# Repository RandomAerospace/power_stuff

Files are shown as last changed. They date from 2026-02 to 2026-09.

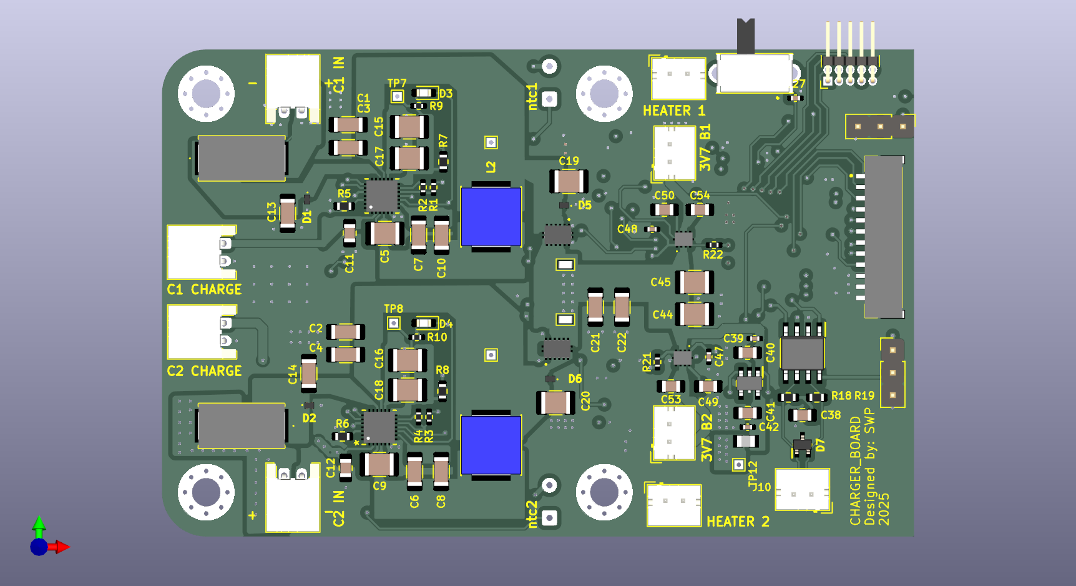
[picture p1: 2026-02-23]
POWER_DISTRIBUTION/SOLAR CHARGER/IMAGES AND RENDERS/SOLAR CHARGER-Top.png

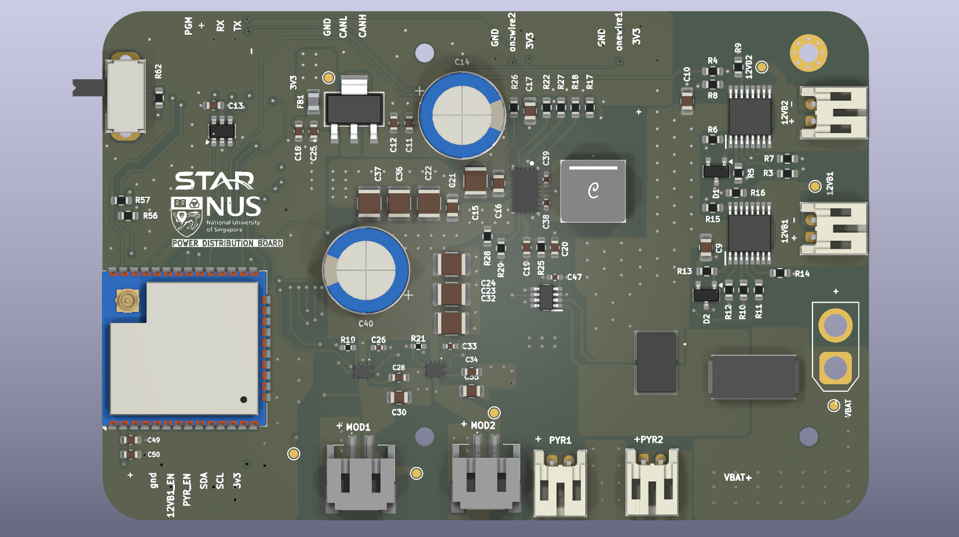
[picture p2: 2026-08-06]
POWER_DISTRIBUTION/UREX_PDB/UREX_PDB/FRONT_PDBr1.png

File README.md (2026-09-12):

if you want to add more stuff, use library loader and set path of downloaded footprints to SAMACSYS_LIB_PDB on my repo!
additionally, please set path preferences based on relative path of the folder that you have pulled the github repo into.
Go to UREX PDB  folder under POWER DISTRIBUTION for the pimped up weather balloon PDB

Power board presentation:https://drive.google.com/file/d/1bSlgJGe3XdCi3mun8Qso9A9fgnM_BNgd/view?usp=sharing

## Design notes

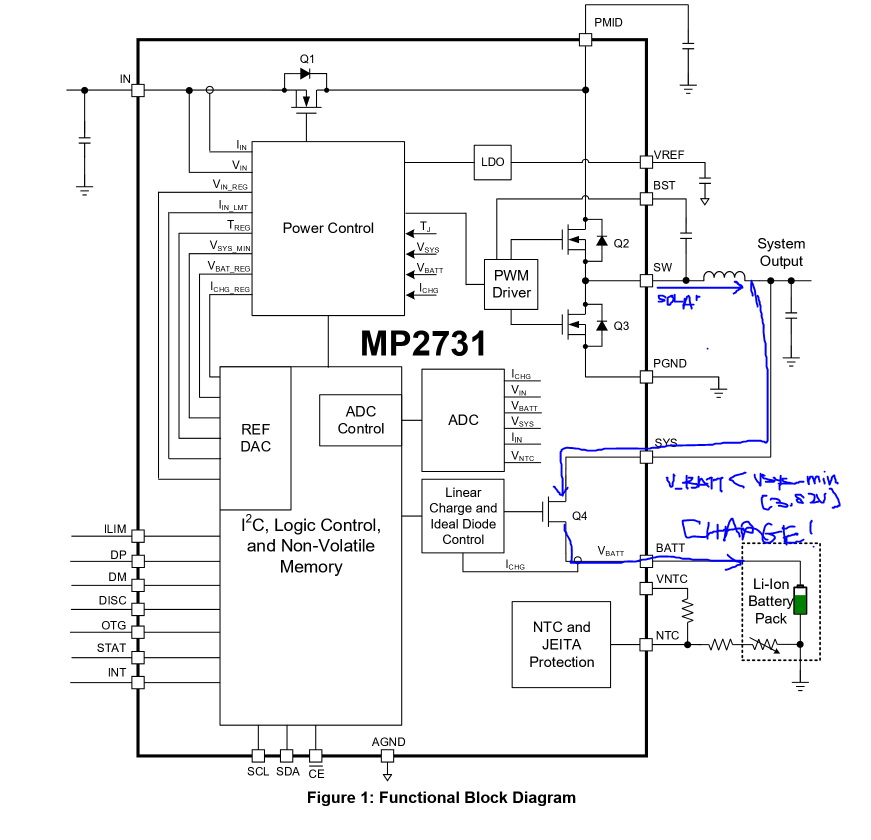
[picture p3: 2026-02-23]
DATASHEETS/CHARGE!.PNG

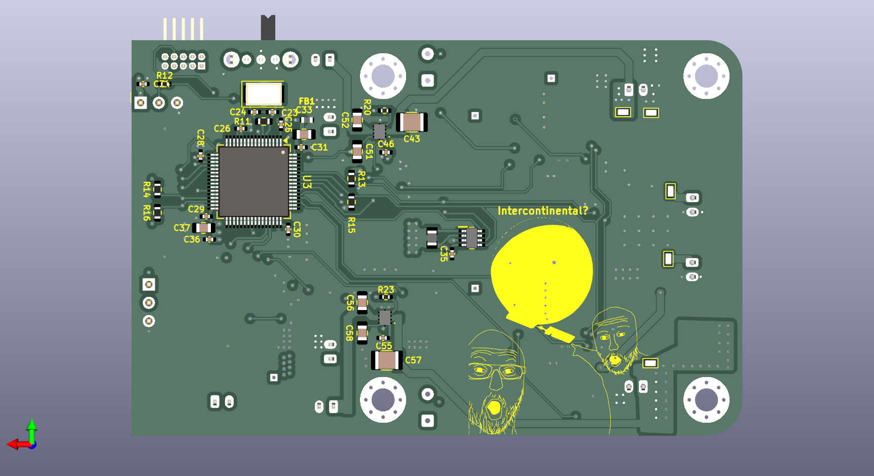
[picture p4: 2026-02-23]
POWER_DISTRIBUTION/SOLAR CHARGER/IMAGES AND RENDERS/SOLAR CHARGER-bottom.png

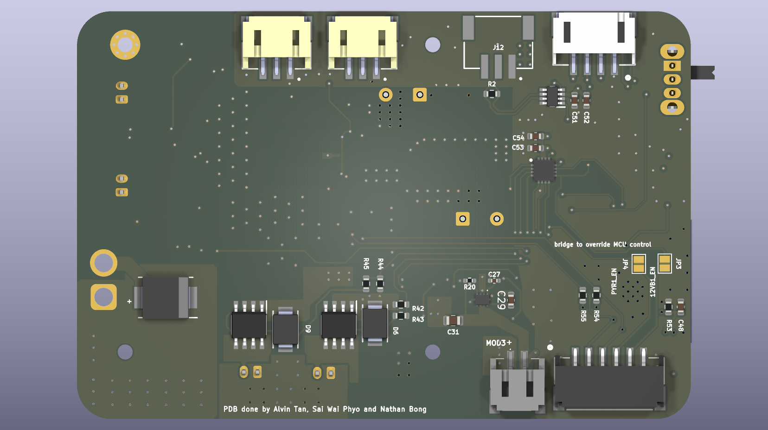
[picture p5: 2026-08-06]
POWER_DISTRIBUTION/UREX_PDB/UREX_PDB/BACK_PDBr1.png

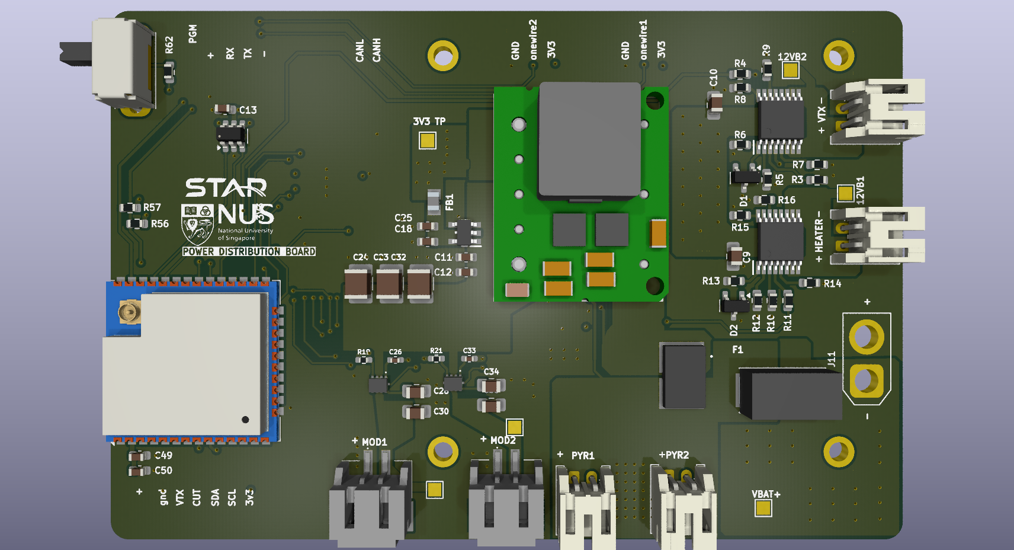
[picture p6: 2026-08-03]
POWER_DISTRIBUTION/UREX_PDB/UREX_PDB/BACK__PDB.png

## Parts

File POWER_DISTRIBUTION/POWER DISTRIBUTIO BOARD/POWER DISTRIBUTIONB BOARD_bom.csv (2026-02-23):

Id | Designator | Footprint | Quantity | Designation | Supplier and ref
1 | TP4,TP5,TP3,TP6,TP8,TP24,TP7 | S175146R | 7 | S1751-46R
2 | F2,F1,F3 | 0154001.DRT | 3 | 0154010.DR
3 | C31,C34,C33,C32 | C_Radial_D6.3mm_H5.0mm_P2.50mm | 4 | 47u
4 | J25,J26,J28,J27 | XT90PWF | 4 | XT90PW-F
5 | J7,J4,J1 | AMASS_XT60-F_1x02_P7.20mm_Vertical | 3 | Conn_01x02_Socket
6 | PS3,PS4 | RPMA5080OF | 2 | RPMA5.0-8.0_OF
7 | U3,U2 | 17861650002 | 2 | 178.6165.0002
8 | R52 | R_0805_2012Metric_Pad1.20x1.40mm_HandSolder | 1 | 8k66
9 | R51 | R_0805_2012Metric_Pad1.20x1.40mm_HandSolder | 1 | 1k82

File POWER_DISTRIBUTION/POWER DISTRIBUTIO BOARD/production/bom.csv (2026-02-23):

Designator | Footprint | Quantity | Value | LCSC Part #
C31, C32, C33, C34 | C_Radial_D6.3mm_H5.0mm_P2.50mm | 4 | 47u
F1, F2, F3 | 0154001.DRT | 3 | 0154010.DR
J1, J4, J7 | AMASS_XT60-F_1x02_P7.20mm_Vertical | 3 | Conn_01x02_Socket
J25, J26, J27, J28 | XT90PWF | 4 | XT90PW-F
PS3, PS4 | RPMA5080OF | 2 | RPMA5.0-8.0_OF
R51 | 0805 | 1 | 1k82
R52 | 0805 | 1 | 8k66
TP24, TP3, TP4, TP5, TP6, TP7, TP8 | S175146R | 7 | S1751-46R
U2, U3 | 17861650002 | 2 | 178.6165.0002

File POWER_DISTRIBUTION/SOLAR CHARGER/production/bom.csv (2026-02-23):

Designator | Footprint | Quantity | Value | LCSC Part #
C1, C10, C13, C14, C2, C21, C22, C3, C4, C6, C7, C8 | 1206 | 12 | 47uF @16VDC
C11, C12, C33, C37, C38, C40, C41, C49, C50, C51, C52, C53, C54, C56, C58 | 0805 | 15 | 1uF @50V
C15, C16, C17, C18, C19, C20, C43, C44, C45, C5, C57, C9 | 1210 | 12 | 10uF @50V
C23, C24 | 0402 | 2 | 20p
C25, C26, C27, C28, C29, C30, C31, C34, C35, C36, C39, C42, C46, C47, C48, C55 | 0402 | 16 | 100nF @50V
D1, D2, D5, D6 | PESD5V0S1BL315 | 4 | PTVS3V3D1BALYL
D3, D4 | 0603 | 2 | LED
D7 | SOT65P210X110-3N | 1 | PESD2CANFD24V-UX
F1, F2 | 0154005DR | 2 | 0154005.DR
FB1 | BLM18SP221SN1B | 1 | BLM18AG601SN1D
FB2 | BEADC2012X105N | 1 | BLM21PG221SN1D
IC1, IC2 | LTC4451AVTRMPBF | 2 | LTC4451AV#TRMPBF
IC3 | SOT65P280X110-8N | 1 | INA232AIDDFR
IC4 | SOIC127P600X175-8N | 1 | SN65HVD233QDRQ1
IC5, IC6, IC7, IC8 | TPS22997RYZR | 4 | TPS22997RYZR
J1 | PinHeader_1x03_P2.54mm_Vertical | 1 | Conn_01x03_Socket
J10, J12, J13, J14, J15 | JST_PH_B2B-PH-K_1x02_P2.00mm_Vertical | 5 | Conn_01x02
J11 | PinHeader_1x03_P2.54mm_Vertical | 1 | Conn_01x03
J18 | BM12BGHSTBTLFSN | 1 | BM12B-GHS-TBT_LF__SN_
J2 | PinHeader_2x05_P1.27mm_Horizontal | 1 | Conn_ARM_JTAG_SWD_10
J3, J5, J6, J7 | JST_PH_S2B-PH-K_1x02_P2.00mm_Horizontal | 4 | Conn_01x02
J8, J9 | SolderWire-0.127sqmm_1x02_P3.7mm_D0.48mm_OD1mm | 2 | Conn_01x02
L1, L2 | INDPM6868X420N | 2 | SRR6838A-1R0Y
PS1 | SOT95P280X145-5N | 1 | TLV75733PDBVR
R1, R10, R12, R2, R20, R21, R22, R23, R3, R4, R9 | 0402 | 11 | 10k
R11 | 0603 | 1 | 1M
R13, R14, R15, R16 | 0603 | 4 | 2.4k
R17 | RESC2013X58N | 1 | WSLP08059L000FEA18
R18, R19 | 0603 | 2 | 60
R5, R6 | 0603 | 2 | 20K
R7, R8 | 0603 | 2 | 100K
S1 | OS102011MA1QN1 | 1 | OS102011MA1QN1
TP1, TP12, TP2, TP7, TP8 | TestPoint_THTPad_1.0x1.0mm_Drill0.5mm | 5 | TestPoint_Alt
TP10, TP11, TP14, TP15, TP16, TP17, TP9 | S276146R | 7 | S2761-46R
U1, U2 | QFN-26_MP2731 | 2 | MP2731GQC-0000-P
U3 | LQFP-64_10x10mm_P0.5mm | 1 | STM32F103RGTx
Y1 | Crystal_SMD_5032-2Pin_5.0x3.2mm | 1 | Crystal

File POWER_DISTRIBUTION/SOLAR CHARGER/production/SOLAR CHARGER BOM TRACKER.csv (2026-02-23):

 | Mouser No | Mfr. No | Manufacturer | Customer No | Description | RoHS | Lifecycle | Order Qty. | Price (SGD) | Ext.: (SGD)
1 | 81-GRM1555C1H200GA1D | GRM1555C1H200GA01D | Murata |  | Multilayer Ceramic Capacitors MLCC - SMD/SMT 20 pF 50 VDC 2% 0402 C0G (NP0) | RoHS Compliant |  | 100 | $0.051 | $5.10
2 | 81-GRM155R61H104KE9J | GRM155R61H104KE19J | Murata |  | Multilayer Ceramic Capacitors MLCC - SMD/SMT 0.1 uF 50 VDC 10% 0402 X5R | RoHS Compliant |  | 500 | $0.025 | $12.50
3 | 81-GRT21BR71H105KE1K | GRT21BR71H105KE01K | Murata |  | Multilayer Ceramic Capacitors MLCC - SMD/SMT 1 uF 50 VDC 10% 0805 X7R AEC-Q200 |  |  | 100 | $0.097 | $9.70
4 | 71-WSLP08059L000FEA1 | WSLP08059L000FEA18 | Vishay |  | Current Sense Resistors - SMD 1watt 0.009ohm 1% | RoHS Compliant |  | 10 | $1.43 | $14.30
5 | 652-SRR6838A-1R0Y | SRR6838A-1R0Y | Bourns |  | Power Inductors - SMD Ind,6.8x6.8x3.8mm,1uH+/-30%,4.5A, | RoHS Compliant | New Product | 10 | $1.60 | $16.00
6 | 595-INA232AIDDFR | INA232AIDDFR | Texas Instruments |  | Current & Power Monitors & Regulators 48-V 16-bit high-pr ecision I C output d | RoHS Compliant |  | 10 | $1.85 | $18.50
7 | 595-TPS22997RYZR | TPS22997RYZR | Texas Instruments |  | Power Switch ICs - Power Distribution 5.5-V 10-A 4-mohm on -resistance load swi | RoHS Compliant |  | 5 | $1.04 | $5.20

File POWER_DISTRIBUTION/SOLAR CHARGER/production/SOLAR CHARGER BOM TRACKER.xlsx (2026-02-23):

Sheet: SOLAR CHARGER_BOM
Reference | Value | Footprint | Datasheet | Qty | DNP | Exclude from BOM | Exclude from Board
R7,R8 | CRCW0603100KFKEA | Resistor_SMD:R_0603_1608Metric | 100K | 2
R1,R2,R3,R4,R9,R10,R12,R20,R21,R22,R23 | CRCW040210K0FKED | Resistor_SMD:R_0402_1005Metric_Pad0.72x0.64mm_HandSolder | 10k | 11
C23,C24 | GRM1555C1H200GA01D | Capacitor_SMD:C_0402_1005Metric_Pad0.74x0.62mm_HandSolder | 20p | 2
C25,C26,C27,C28,C29,C30,C31,C34,C35,C36,C39,C42,C46,C47,C48,C55 | GRM155R61H104KE19J | Capacitor_SMD:C_0402_1005Metric_Pad0.74x0.62mm_HandSolder | 100nF @50V | 16
C1,C2,C3,C4,C6,C7,C8,C10,C13,C14,C21,C22 | GRM31CR61C476ME44L | Capacitor_SMD:C_1206_3216Metric_Pad1.33x1.80mm_HandSolder | 47uF @16VDC | 12
C5,C9,C15,C16,C17,C18,C19,C20,C43,C44,C45,C57 | GRM32EC72A106KE05L | Capacitor_SMD:C_1210_3225Metric_Pad1.33x2.70mm_HandSolder | 10uF @50V | 12
C11,C12,C33,C37,C38,C40,C41,C49,C50,C51,C52,C53,C54,C56,C58 | GRT21BR71H105KE01K | Capacitor_SMD:C_0805_2012Metric_Pad1.18x1.45mm_HandSolder | 1uF @50V | 15
J2 | Conn_ARM_JTAG_SWD_10 | Connector_PinHeader_1.27mm:PinHeader_2x05_P1.27mm_Horizontal | http://infocenter.arm.com/help/topic/com.arm.doc.ddi0314h/DDI0314H_coresight_components_trm.pdf | 1
J18 | BM12B-GHS-TBT_LF__SN_ | samac_sys:BM12BGHSTBTLFSN | http://www.jst-mfg.com/product/pdf/eng/eGH.pdf | 1
FB1 | BLM18AG601SN1D | samac_sys:BLM18SP221SN1B | http://www.murata.com/~/media/webrenewal/support/library/catalog/products/emc/emifil/c31e.ashx?la=en-gb | 1
IC4 | SN65HVD233QDRQ1 | samac_sys:SOIC127P600X175-8N | http://www.ti.com/lit/gpn/sn65hvd233-q1 | 1
PS1 | TLV75733PDBVR | samac_sys:SOT95P280X145-5N | http://www.ti.com/lit/gpn/tlv757p | 1
D7 | PESD2CANFD24V-UX | samac_sys:SOT65P210X110-3N | https://assets.nexperia.com/documents/data-sheet/PESD2CANFD24V-U.pdf | 1
D1,D2,D5,D6 | PTVS3V3D1BALYL | samac_sys:PESD5V0S1BL315 | https://assets.nexperia.com/documents/data-sheet/PTVS3V3D1BAL.pdf | 4
FB2 | BLM21PG221SN1D | samac_sys:BEADC2012X105N | https://datasheet.datasheetarchive.com/originals/dk/DKDS-31/605570.pdf | 1
L1,L2 | SRR6838A-1R0Y | samac_sys:INDPM6868X420N | https://g.componentsearchengine.com/Datasheets/0/20314705.pdf | 2
IC1,IC2 | LTC4451AV#TRMPBF | samac_sys:LTC4451AVTRMPBF | https://www.analog.com/media/en/technical-documentation/data-sheets/ltc4451.pdf | 2
S1 | OS102011MA1QN1 | samac_sys:OS102011MA1QN1 | https://www.ckswitches.com/media/1428/os.pdf | 1
F1,F2 | 0154005.DR | samac_sys:0154005DR | https://www.littelfuse.com/~/media/electronics/datasheets/fuses/littelfuse_fuse_154_154t_154l_154tl_datasheet.pdf.pdf | 2
TP9,TP10,TP11,TP14,TP15,TP16,TP17 | S2761-46R | samac_sys:S276146R | https://www.mouser.fr/ProductDetail/Harwin/S2761-46R?qs=DaxoyN%2FvrebHvZaagZ7Fog%3D%3D | 7
U3 | STM32F103RGTx | Package_QFP:LQFP-64_10x10mm_P0.5mm | https://www.st.com/resource/en/datasheet/stm32f103rg.pdf | 1
IC3 | INA232AIDDFR | samac_sys:SOT65P280X110-8N | https://www.ti.com/lit/ds/symlink/ina232.pdf?ts=1678135005205 | 1
IC5,IC6,IC7,IC8 | TPS22997RYZR | samac_sys:TPS22997RYZR | https://www.ti.com/lit/gpn/tps22997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 | 4
R17 | WSLP08059L000FEA18 | samac_sys:RESC2013X58N | https://www.vishay.com/docs/30298/wslp18.pdf | 1
U1,U2 | MP2731GQC-0000-P | MP2731:QFN-26_MP2731 |  | 2
R18,R19 | RK73H1HRTTCM60R4F | Resistor_SMD:R_0603_1608Metric |  | 2
Y1 | X50328MSB2GI | Crystal:Crystal_SMD_5032-2Pin_5.0x3.2mm |  | 1
D3,D4 | LED | LED_SMD:LED_0603_1608Metric_Pad1.05x0.95mm_HandSolder | ~ | 2
H1,H2,H3,H4 | MountingHole_Pad | MountingHole:MountingHole_3.2mm_M3_Pad_Via | ~ | 4 |  | Excluded from BOM
J1 | Conn_01x03_Socket | Connector_PinHeader_2.54mm:PinHeader_1x03_P2.54mm_Vertical | ~ | 1
J3,J5,J6,J7 | Conn_01x02 | Connector_JST:JST_PH_S2B-PH-K_1x02_P2.00mm_Horizontal | ~ | 4
J8,J9 | Conn_01x02 | Connector_Wire:SolderWire-0.127sqmm_1x02_P3.7mm_D0.48mm_OD1mm | ~ | 2
J10,J12,J13,J14,J15 | Conn_01x02 | Connector_JST:JST_PH_B2B-PH-K_1x02_P2.00mm_Vertical | ~ | 5
J11 | Conn_01x03 | Connector_PinHeader_2.54mm:PinHeader_1x03_P2.54mm_Vertical | ~ | 1
R5,R6 | 20K | Resistor_SMD:R_0603_1608Metric | ~ | 2
R11 | 1M | Resistor_SMD:R_0603_1608Metric | ~ | 1
R13,R14,R15,R16 | 2.4k | Resistor_SMD:R_0603_1608Metric | ~ | 4
TP1,TP2,TP7,TP8,TP12 | TestPoint_Alt | TestPoint:TestPoint_THTPad_1.0x1.0mm_Drill0.5mm | ~ | 5
TP3,TP4,TP5,TP6 | TestPoint_Alt | TestPoint:TestPoint_THTPad_1.0x1.0mm_Drill0.5mm | ~ | 4 | DNP | Excluded from BOM | Excluded from board

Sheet: LCSC
LCSC Part Number | Manufacture Part Number | Manufacturer | Customer NO. | Package | Description | RoHS | Quantity | Unit Price($) | Ext.Price($) | Estimated lead time (business days) | Date Code / Lot No. | Status
C844916 | CRCW0603100KFKEA | VISHAY | R7,R8 | 0603 | 100mW Thick Film Resistor 75V Â±1% Â±100ppm/â„ƒ 100kÎ© 0603 Chip Resistor - Surface Mount ROHS | YES | 500 | 0.0041 | 2.05 |  |  | -
C71617 | CRCW040210K0FKED | VISHAY | R1,R2,R3,R4,R9,R10,R12,R20,R21,R22,R23 | 0402 | 63mW Thick Film Resistor 50V Â±1% Â±100ppm/â„ƒ 10kÎ© 0402 Chip Resistor - Surface Mount ROHS | YES | 500 | 0.0031 | 1.55 |  |  | -
C385047 | GRM31CR61C476ME44L | muRata | C1,C2,C3,C4,C6,C7,C8,C10,C13,C14,C21,C22 | 1206 | 16V 47uF X5R Â±20% 1206 Multilayer Ceramic Capacitors MLCC - SMD/SMT ROHS | YES | 200 | 0.2449 | 48.98 |  |  | -
C576517 | GRM32EC72A106KE05L | muRata | C5,C9,C15,C16,C17,C18,C19,C20,C43,C44,C45,C57 | 1210 | 100V 10uF X7S Â±10% 1210 Multilayer Ceramic Capacitors MLCC - SMD/SMT ROHS | YES | 200 | 0.2366 | 47.32 |  |  | -
C19330 | BLM18AG601SN1D | muRata | FB1 | 0603 | 380mÎ© Â±25% 600Î©@100MHz 0603 Ferrite Beads ROHS | YES | 1000 | 0.0048 | 4.8 |  |  | -
C552487 | PESD2CANFD24V-UX | Nexperia | D7 | SOT-323 | 2.6A@8/20us 42V 25.5V Bidirectional 24V SOT-323 ESD and Surge Protection (TVS/ESD) ROHS | YES | 500 | 0.0585 | 29.25 |  |  | -
C553419 | PTVS3V3D1BALYL | Nexperia | D1,D2,D5,D6 | DFN1006-2 | 34A@8/20us 13.2V 4.5V Bidirectional 3.3V DFN1006-2 ESD and Surge Protection (TVS/ESD) ROHS | YES | 500 | 0.0393 | 19.65 |  |  | -
C85840 | BLM21PG221SN1D | muRata | FB2 | 0805 | 45mÎ© Â±25% 220Î©@100MHz 0805 Ferrite Beads ROHS | YES | 1000 | 0.0129 | 12.9 |  |  | -
C226259 | OS102011MA1QN1 | C&K | S1 | Through Hole | 100mA SPDT 12V 10,000 Cycles Through Hole Slide Switches ROHS | YES | 50 | 0.3818 | 19.09 |  |  | -
C206916 | 0154005.DR | Littelfuse | F1,F2 | SMD,9.7x5mm | 50A SMD Fuseï¼ˆwith Holderï¼‰ 5A 125V 125V SMD,9.7x5mm Disposable fuses ROHS | YES | 30 | 1.006 | 30.18 |  |  | -
C5846954 | S2761-46R | Harwin | TP9,TP10,TP11,TP14,TP15,TP16,TP17 | - | Test Points / Test Rings ROHS | YES | 100 | 0.2157 | 21.57 |  |  | -
C115962 | X50328MSB2GI | YXC Crystal Oscillators | Y1 | SMD5032-2P | 8MHz Crystal Oscillator 20pF Â±10ppm Â±20ppm SMD5032-2P Crystals ROHS | YES | 100 | 0.147 | 14.7 |  |  | -
C15742 | STM32F405RGT6 | ST |  | LQFP-64(10x10) | ARM-M4 168MHz LQFP-64(10x10) Microcontrollers (MCU/MPU/SOC) ROHS | YES | 10 | 2.8768 | 28.77 |  |  | -

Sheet: Mouser_Cart
1 | 81-GRM1555C1H200GA1D | GRM1555C1H200GA01D | Murata | Multilayer Ceramic Capacitors MLCC - SMD/SMT 20 pF 50 VDC 2% 0402 C0G (NP0) | RoHS Compliant |  | 100 | $0.051 | $5.10
2 | 81-GRM155R61H104KE9J | GRM155R61H104KE19J | Murata | Multilayer Ceramic Capacitors MLCC - SMD/SMT 0.1 uF 50 VDC 10% 0402 X5R | RoHS Compliant |  | 500 | $0.025 | $12.50
3 | 81-GRT21BR71H105KE1K | GRT21BR71H105KE01K | Murata | Multilayer Ceramic Capacitors MLCC - SMD/SMT 1 uF 50 VDC 10% 0805 X7R AEC-Q200 |  |  | 100 | $0.097 | $9.70
4 | 71-WSLP08059L000FEA1 | WSLP08059L000FEA18 | Vishay | Current Sense Resistors - SMD 1watt 0.009ohm 1% | RoHS Compliant |  | 10 | $1.43 | $14.30
5 | 652-SRR6838A-1R0Y | SRR6838A-1R0Y | Bourns | Power Inductors - SMD Ind,6.8x6.8x3.8mm,1uH+/-30%,4.5A, | RoHS Compliant | New Product | 10 | $1.60 | $16.00
6 | 595-INA232AIDDFR | INA232AIDDFR | Texas Instruments | Current & Power Monitors & Regulators 48-V 16-bit high-pr ecision I C output d | RoHS Compliant |  | 10 | $1.85 | $18.50
7 | 595-TPS22997RYZR | TPS22997RYZR | Texas Instruments | Power Switch ICs - Power Distribution 5.5-V 10-A 4-mohm on -resistance load swi | RoHS Compliant |  | 5 | $1.04 | $5.20

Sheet: pdb_bom
Reference | Value |  | Footprint | Datasheet | Qty
C1,C2 | 10uF @50V | GRM32EC72A106KE05L | Capacitor_SMD:C_1210_3225Metric_Pad1.33x2.70mm_HandSolder |  | 2
C3,C4,C21,C23,C25,C26,C39 | 100nF @50V | GRM155R61H104KE19J | Capacitor_SMD:C_0402_1005Metric_Pad0.74x0.62mm_HandSolder |  | 7
C5,C6,C7,C8,C9,C10,C11,C12 | 1uF @50V | GRT21BR71H105KE01K | Capacitor_SMD:C_0805_2012Metric_Pad1.18x1.45mm_HandSolder |  | 8
C17,C18,C20,C27,C28,C35,C36 | 47uF @16VDC | GRM31CR61C476ME44L | Capacitor_SMD:C_1206_3216Metric_Pad1.33x1.80mm_HandSolder |  | 7
C19 | 4.7uF @50V | GRM31CR71H475KA12L | Capacitor_SMD:C_1206_3216Metric_Pad1.33x1.80mm_HandSolder |  | 1
C22 | 6.8nF @50V | GCM188R71H682KA37D | Capacitor_SMD:C_0603_1608Metric_Pad1.08x0.95mm_HandSolder |  | 1
C24 | 22nF @25V | GRM155R71E223KA61 | Capacitor_SMD:C_0402_1005Metric_Pad0.74x0.62mm_HandSolder |  | 1
C29 | 150pF @50V | GRM1555C1H151GA01 | Capacitor_SMD:C_0402_1005Metric_Pad0.74x0.62mm_HandSolder |  | 1
C30,C31,C33 | 47uF @16VDC | CGA9N3X7R1C476M230KB | Capacitor_SMD:C_2220_5750Metric_Pad1.97x5.40mm_HandSolder |  | 3
D1,D2,D3,D4 |  | BAS21 | Package_TO_SOT_SMD:SOT-23 | https://www.diodes.com/assets/Datasheets/Ds12004.pdf | 4
D9,D10,D11,D12 |  | SMBJ12CA | SamacSys_Parts:DIONM5436X244N |  | 4
IC1,IC2 |  | TPS22997RYZR | SamacSys_Parts:TPS22997RYZR | https://www.ti.com/lit/gpn/tps22997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 | 2
IC3,IC4,IC5,IC6 |  | TPS1HB08BQPWPRQ1 | SamacSys_Parts:SOP65P640X120-17N | https://www.ti.com/lit/gpn/TPS1HB08-Q1 | 4
IC11 |  | TPS56837RPAR | SamacSys_Parts:TPS56A37RPAR | https://www.ti.com/lit/gpn/tps56837 | 1
IC12 |  | INA232AIDDFR | SamacSys_Parts:SOT65P280X110-8N | https://www.ti.com/lit/ds/symlink/ina232.pdf?ts=1678135005205 | 1
J1,J2,J3,J4,J6,J7,J8,J13,J14,J15 | 43650-0211 |  | SamacSys_Parts:43650-02YY_091011 | https://www.molex.com/pdm_docs/sd/436500209_sd.pdf | 10
J9,J10,J11,J12 | 43650-0312 |  | Connector_Molex:Molex_Micro-Fit_3.0_43650-0300_1x03_P3.00mm_Horizontal | https://www.molex.com/pdm_docs/sd/436500212_sd.pdf | 4
J16 | Conn_01x02 |  | Connector_AMASS:AMASS_XT30PW-M_1x02_P2.50mm_Horizontal | ~ | 1
J17,J18 |  | BM12B-GHS-TBT_LF__SN_ | BM12BGHSTBTLFSN | http://www.jst-mfg.com/product/pdf/eng/eGH.pdf | 2
L1 |  | IHLP4040DZER3R3M01 | SamacSys_Parts:INDPM108102X400N | https://www.vishay.com/docs/34193/ihlp-4040dz-01.pdf | 1
L2 | 78439358047 |  | SamacSys_Parts:78439358047 |  | 1
Q1,Q2,Q3,Q4 |  | IPD047N03LF2SATMA1 | SamacSys_Parts:IPD047N03LF2SATMA1 | https://www.infineon.com/cms/en/product/power/mosfet/n-channel/ipd047n03lf2s/ | 4
R1,R2 | 10k | CRCW040210K0FKED | Resistor_SMD:R_0402_1005Metric_Pad0.72x0.64mm_HandSolder |  | 2
R3,R4,R8,R9,R10,R11,R15,R16,R17,R18,R19,R20,R27,R28,R29,R30 | 15k | ~ | Resistor_SMD:R_0603_1608Metric |  | 16
R5,R12,R21,R22 | 1K |  | Resistor_SMD:R_0603_1608Metric | ~ | 4
R6,R13,R23,R25 | 4.7k |  | Resistor_SMD:R_0603_1608Metric | ~ | 4
R7,R14,R24,R26 | 13.3k |  | Resistor_SMD:R_0603_1608Metric | ~ | 4
R59 | 20k |  | Resistor_SMD:R_0603_1608Metric | ~ | 1
R60 | 130k |  | Resistor_SMD:R_0603_1608Metric | ~ | 1
R61 | 6.8k |  | Resistor_SMD:R_0603_1608Metric | ~ | 1
R62,R69 | 30K | CRCW040230K1FKED | Resistor_SMD:R_0402_1005Metric_Pad0.72x0.64mm_HandSolder |  | 2
R63 | 750k |  | Resistor_SMD:R_0603_1608Metric | ~ | 1
R64 | 68K |  | Resistor_SMD:R_0603_1608Metric | ~ | 1
R65 | 10K |  | Resistor_SMD:R_0603_1608Metric | ~ | 1
R66 | 100K | CRCW0603100KFKEA | Resistor_SMD:R_0603_1608Metric |  | 1
R67 | 27k |  | Resistor_SMD:R_0603_1608Metric | ~ | 1
R68 | 73.2K | CRCW060373K2FKEA | Resistor_SMD:R_0603_1608Metric |  | 1
R70,R72,R74,R76 | 10M |  | Resistor_SMD:R_0603_1608Metric | ~ | 4
R71,R73,R75,R77 | 2k |  | Resistor_SMD:R_0603_1608Metric | ~ | 4
R78 |  | WSHM28186L800FEA | SamacSys_Parts:WSHM2818R0330FEB | https://componentsearchengine.com/Datasheets/2/WSHM2818R0330FEB.pdf | 1
TP2,TP3,TP5,TP6,TP7,TP8,TP9,TP10,TP11,TP12,TP13,TP14,TP15,TP16,TP17 |  | S2761-46R | SamacSys_Parts:S276146R | https://www.mouser.fr/ProductDetail/Harwin/S2761-46R?qs=DaxoyN%2FvrebHvZaagZ7Fog%3D%3D | 15
TP18,TP19 |  | S2761-46R | samac_sys:S276146R | https://www.mouser.fr/ProductDetail/Harwin/S2761-46R?qs=DaxoyN%2FvrebHvZaagZ7Fog%3D%3D | 2
U1 |  | MP3432GL-P | MP3432GL:QFN-3x4_MP3432_MNP | MP3432GL-P | 1

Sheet: Cappies
Used in all designs | Remarks |  | Bought |  |  | Requires Purchase |  | Used in PDB
GRM32EC72A106KE05L | 10uF @50V | Capacitor_SMD:C_1210_3225Metric_Pad1.33x2.70mm_HandSolder | GRM31CR61C476ME44L |  | 200 | GRM155R61H104KE19J | 7 | GRM32EC72A106KE05L | 2
GRM155R61H104KE19J | 100nF @50V | Capacitor_SMD:C_0402_1005Metric_Pad0.74x0.62mm_HandSolder | GRM32EC72A106KE05L |  | 200 | GRT21BR71H105KE01K | 8 | GRM155R61H104KE19J | 7
GRT21BR71H105KE01K | 1uF @50V | Capacitor_SMD:C_0805_2012Metric_Pad1.18x1.45mm_HandSolder |  |  |  | GRM31CR71H475KA12L | 1 | GRT21BR71H105KE01K | 8
GRM31CR61C476ME44L | 47uF @16VDC | Capacitor_SMD:C_1206_3216Metric_Pad1.33x1.80mm_HandSolder |  |  |  | GCM188R71H682KA37D | 1 | GRM31CR61C476ME44L | 7
GRM31CR71H475KA12L | 4.7uF @50V | Capacitor_SMD:C_1206_3216Metric_Pad1.33x1.80mm_HandSolder |  |  |  | GRM155R71E223KA61 | 1 | GRM31CR71H475KA12L | 1
GCM188R71H682KA37D | 6.8nF @50V | Capacitor_SMD:C_0603_1608Metric_Pad1.08x0.95mm_HandSolder |  |  |  | GRM1555C1H151GA01 | 1 | GCM188R71H682KA37D | 1
GRM155R71E223KA61 | 22nF @25V | Capacitor_SMD:C_0402_1005Metric_Pad0.74x0.62mm_HandSolder |  |  |  | CGA9N3X7R1C476M230KB | 3 | GRM155R71E223KA61 | 1
GRM1555C1H151GA01 | 150pF @50V | Capacitor_SMD:C_0402_1005Metric_Pad0.74x0.62mm_HandSolder |  |  |  |  |  | GRM1555C1H151GA01 | 1
CGA9N3X7R1C476M230KB | 47uF @16VDC | Capacitor_SMD:C_2220_5750Metric_Pad1.97x5.40mm_HandSolder |  |  |  |  |  | CGA9N3X7R1C476M230KB | 3
GRM1555C1H200GA01D | 20p | Capacitor_SMD:C_0402_1005Metric_Pad0.74x0.62mm_HandSolder
SOLAR CHARGER
C1,C2 | 10uF @50V | GRM32EC72A106KE05L | Capacitor_SMD:C_1210_3225Metric_Pad1.33x2.70mm_HandSolder |  | 2
C3,C4,C21,C23,C25,C26,C39 | 100nF @50V | GRM155R61H104KE19J | Capacitor_SMD:C_0402_1005Metric_Pad0.74x0.62mm_HandSolder |  | 7
C5,C6,C7,C8,C9,C10,C11,C12 | 1uF @50V | GRT21BR71H105KE01K | Capacitor_SMD:C_0805_2012Metric_Pad1.18x1.45mm_HandSolder |  | 8
C17,C18,C20,C27,C28,C35,C36 | 47uF @16VDC | GRM31CR61C476ME44L | Capacitor_SMD:C_1206_3216Metric_Pad1.33x1.80mm_HandSolder |  | 7
C19 | 4.7uF @50V | GRM31CR71H475KA12L | Capacitor_SMD:C_1206_3216Metric_Pad1.33x1.80mm_HandSolder |  | 1
C22 | 6.8nF @50V | GCM188R71H682KA37D | Capacitor_SMD:C_0603_1608Metric_Pad1.08x0.95mm_HandSolder |  | 1
C24 | 22nF @25V | GRM155R71E223KA61 | Capacitor_SMD:C_0402_1005Metric_Pad0.74x0.62mm_HandSolder |  | 1
C29 | 150pF @50V | GRM1555C1H151GA01 | Capacitor_SMD:C_0402_1005Metric_Pad0.74x0.62mm_HandSolder |  | 1
C30,C31,C33 | 47uF @16VDC | CGA9N3X7R1C476M230KB | Capacitor_SMD:C_2220_5750Metric_Pad1.97x5.40mm_HandSolder |  | 3
PDB
Reference | Value | Footprint | Datasheet | Qty
C23,C24 | GRM1555C1H200GA01D | Capacitor_SMD:C_0402_1005Metric_Pad0.74x0.62mm_HandSolder | 20p | 2
C25,C26,C27,C28,C29,C30,C31,C34,C35,C36,C39,C42,C46,C47,C48,C55 | GRM155R61H104KE19J | Capacitor_SMD:C_0402_1005Metric_Pad0.74x0.62mm_HandSolder | 100nF @50V | 16
C1,C2,C3,C4,C6,C7,C8,C10,C13,C14,C21,C22 | GRM31CR61C476ME44L | Capacitor_SMD:C_1206_3216Metric_Pad1.33x1.80mm_HandSolder | 47uF @16VDC | 12
C5,C9,C15,C16,C17,C18,C19,C20,C43,C44,C45,C57 | GRM32EC72A106KE05L | Capacitor_SMD:C_1210_3225Metric_Pad1.33x2.70mm_HandSolder | 10uF @50V | 12
C11,C12,C33,C37,C38,C40,C41,C49,C50,C51,C52,C53,C54,C56,C58 | GRT21BR71H105KE01K | Capacitor_SMD:C_0805_2012Metric_Pad1.18x1.45mm_HandSolder | 1uF @50V | 15

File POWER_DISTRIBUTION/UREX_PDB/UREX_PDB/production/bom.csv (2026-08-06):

Designator | Footprint | Quantity | Value | LCSC Part #
C10, C30, C31, C35, C9 | 0805 | 5 | 1uF @50V
C11, C18, C50, C52, C54 | 0603 | 5 | 1uF
C12, C13, C25, C48, C49, C51, C53 | 0603 | 7 | 100nF @50V
C14, C40 | CP_Radial_D10.0mm_P5.00mm | 2 | 330uF@50v
C15 | 1210 | 1 | 10uF@50V
C16, C17 | 0805 | 2 | 4.7uF
C19 | 0603 | 1 | 330pF
C20 | 0603 | 1 | 22nF
C21 | 0805 | 1 | 1uF
C22, C36, C37 | 1210 | 3 | 47uF@16V
C23, C24, C32 | 1210 | 3 | 10uF @50V
C26, C27, C33, C38, C39, C47 | 0402 | 6 | 100nF @50V
C28, C29, C34 | 0603 | 3 | 1nF
D1, D2 | SOT-23 | 2 | BAS21
D6, D9 | DIONM5436X244N | 2 | SMBJ15CA
D7 | DIOM7959X262N | 1 | SSC53L-E3_57T
F1 | 0154005DRL | 1 | 0154005.DRL
FB1 | BEADC2012X105N | 1 | BLM21PG221SN1D
H5, H7, H8 | MountingHole_2.2mm_M2_ISO7380 | 3 | MountingHole_Pad
H6 | MountingHole_2.2mm_M2_Pad_Via | 1 | MountingHole_Pad
IC1 | SOT65P280X110-8N | 1 | TCAN1044VDDFR
IC10, IC8, IC9 | TPS22997RYZR | 3 | TPS22997RYZR
IC2, IC3 | SOP65P640X120-17N | 2 | TPS1HB08BQPWPRQ1
IC4 | SOT65P280X110-8N | 1 | INA232AIDDFR
IC5 | QFN50P300X300X100-17N-D | 1 | TCA6408ARGTR
J10, J4, J7 | S2BPHSM4TBLFSN | 3 | S2B-PH-SM4-TB_LF__SN_
J11 | AMASS_XT30U-F_1x02_P5.0mm_Vertical | 1 | Conn_01x02
J12, J5, J8 | S3BPHSM4TBLFSN | 3 | S3B-PH-SM4-TB_LF__SN_
J33, J34, J36, J37 | JST_PH_S2B-PH-K_1x02_P2.00mm_Horizontal | 4 | Conn_01x02
J6 | S4B-PH-SM4-TB | 1 | S4B-PH-SM4-TB_LF__SN_
J9 | S6B-PH-SM4-TB_LF__SN__3 | 1 | S6B-PH-SM4-TB_LF__SN_
L1 | XAL7070472MEC | 1 | XAL7070-472MEC
Q1, Q2 | SOIC127P600X175-8N | 2 | RSS070N05HZGTB
R1 | WSHM2818R0330FEB | 1 | WSHM28186L800FEA
R10, R11, R15, R16, R3, R4, R8, R9 | 0603 | 8 | 15k
R12, R5, R62 | 0603 | 3 | 1K
R13, R6 | 0603 | 2 | 4.7k
R14, R7 | 0603 | 2 | 13.3k
R17 | 0603 | 1 | 301K
R18, R28 | 0603 | 2 | 100K
R19, R20, R21 | 0402 | 3 | 10k
R2 | 0603 | 1 | 120r
R22, R27 | 0603 | 2 | 102K
R25 | 0603 | 1 | 16.9K
R26 | 0603 | 1 | 48.7k
R29 | 0603 | 1 | 31.6K
R42, R44 | 0603 | 2 | 10M
R43, R45 | 0603 | 2 | 2k
R53 | 0603 | 1 | 10K
R54, R55 | 0603 | 2 | 2K4
R56, R57 | 0603 | 2 | 4k7
S1 | SW_Slide_SPDT_Angled_CK_OS102011MA1Q | 1 | OS102011MA1QN1
TP2, TP3, TP4, TP5, TP6, TP7, TP8 | TestPoint_Pad_D1.0mm | 7 | TestPoint
U1 | ESP32-WROOM-32UE | 1 | ESP32-WROOM-32UE-R2
U4 | SOT-223-4_DCY_TEX | 1 | PLM1117120QDCYRQ1
U5 | RYQ0021A-MFG | 1 | XTPS552892RYQR
U7 | SOT-23-6 | 1 | USBLC6-2SC6

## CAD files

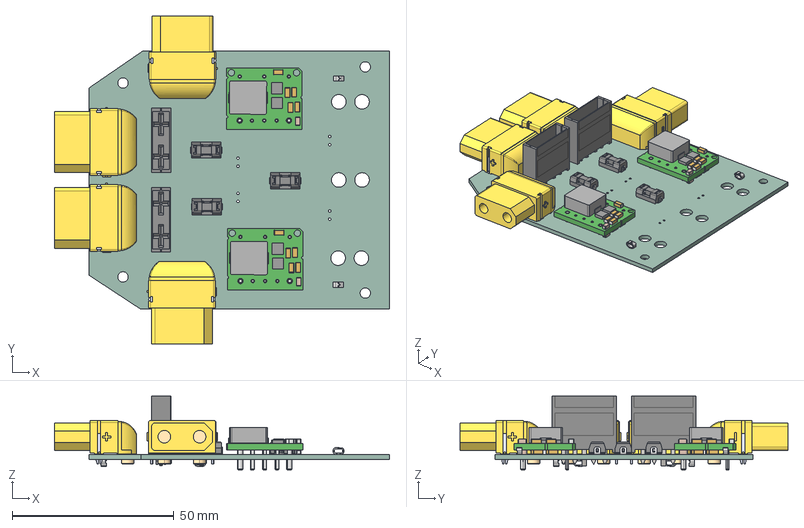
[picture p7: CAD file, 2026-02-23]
POWER_DISTRIBUTION/POWER DISTRIBUTIO BOARD/POWER_CONDITIONING_BOARD.step
103.7 x 101.4 x 22.9 mm
0154010.DR x 3
S1751-46R x 6
XT90PW-F x 4
RPMA5.0-8.0_OF_3D_20210407 x 2
POWER DISTRIBUTIONB BOARD_PCB

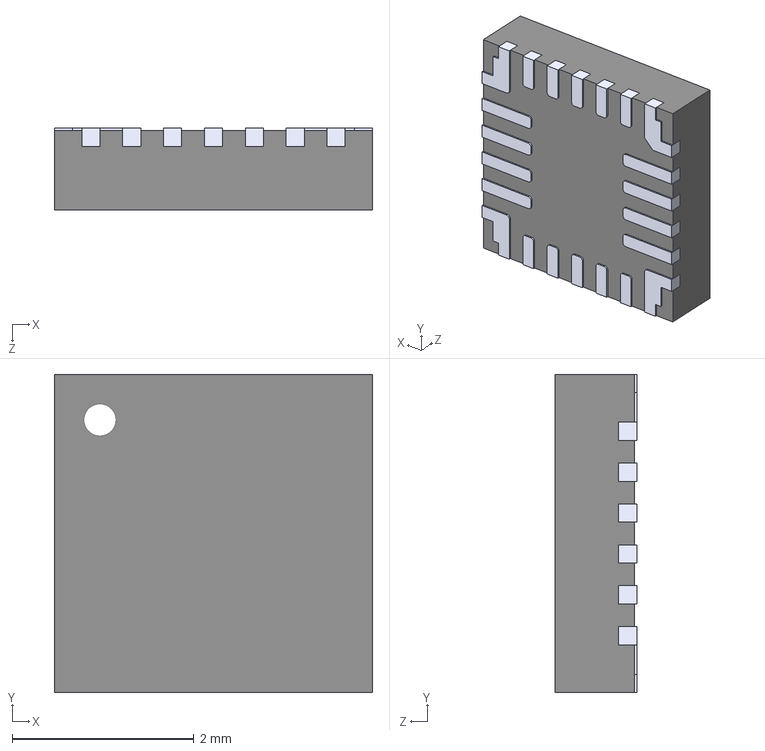
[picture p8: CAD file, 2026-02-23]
SAMACSYS_LIB_PDB/ul_MP2731GQC-0000-P/KiCADv6/MP2731 (QFN-26, 3.5x3.5).step
3.50 x 3.50 x 0.9 mm

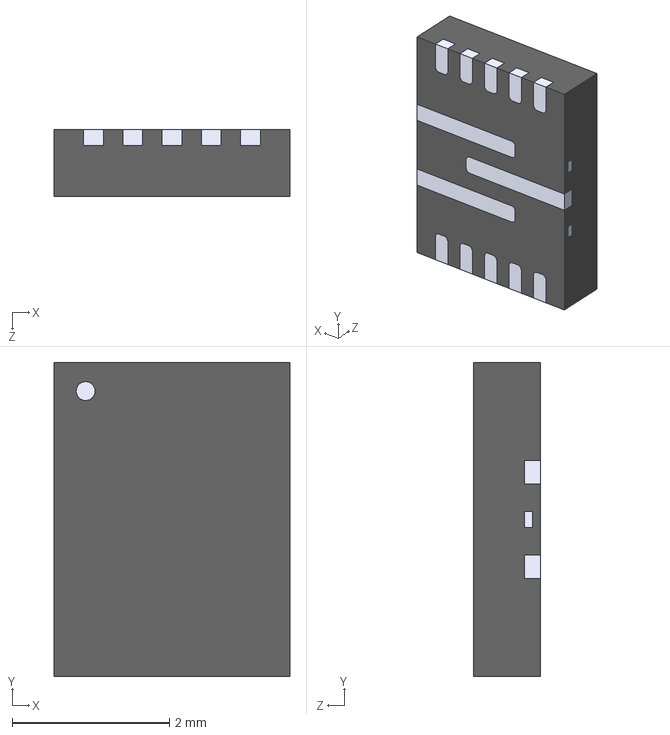
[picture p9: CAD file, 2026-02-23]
SAMACSYS_LIB_PDB/ul_MP3432GL-P/MP3429GL.step
3.00 x 4.00 x 0.85 mm

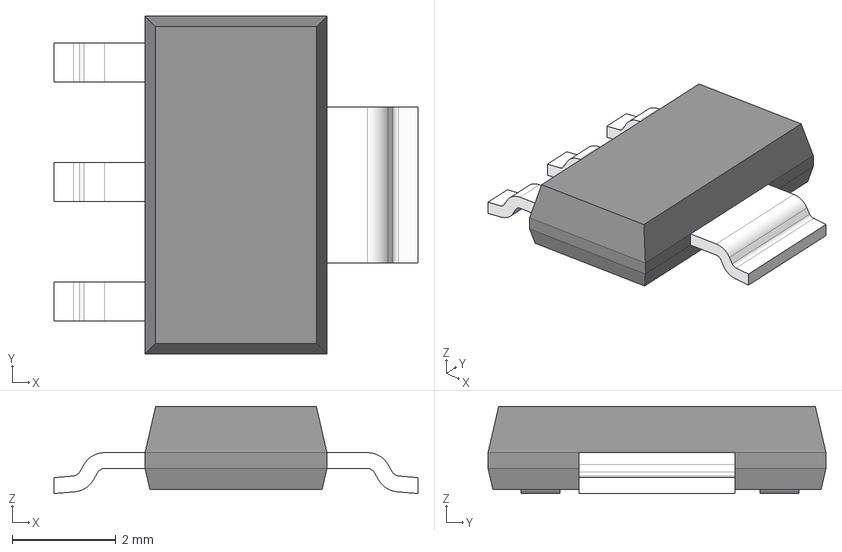
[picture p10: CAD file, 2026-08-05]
SAMACSYS_LIB_PDB/ul_PLM1117120QDCYRQ1/DCY0004A.stp
7.00 x 6.50 x 1.68 mm
BODY-SOT
LEAD-SOT x 3
LEAD-SOT-WIDE
PIN1-ID

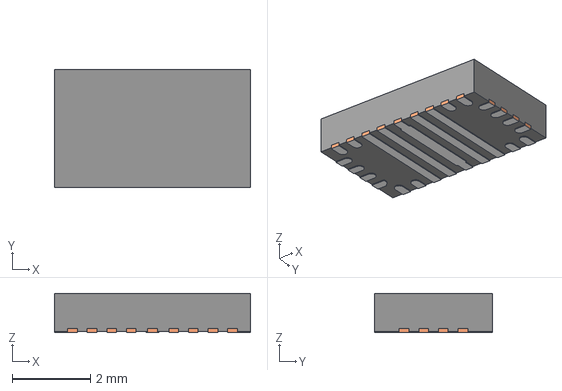
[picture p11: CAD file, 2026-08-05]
SAMACSYS_LIB_PDB/ul_XTPS552892RYQR/RYQ0021A.stp
5.00 x 3.00 x 1.00 mm
BODY-QFN
FRAME-RYQ0021A

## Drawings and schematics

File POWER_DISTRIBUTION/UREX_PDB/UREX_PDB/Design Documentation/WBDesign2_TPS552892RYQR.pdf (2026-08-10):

## WEBENCH ® Design Report

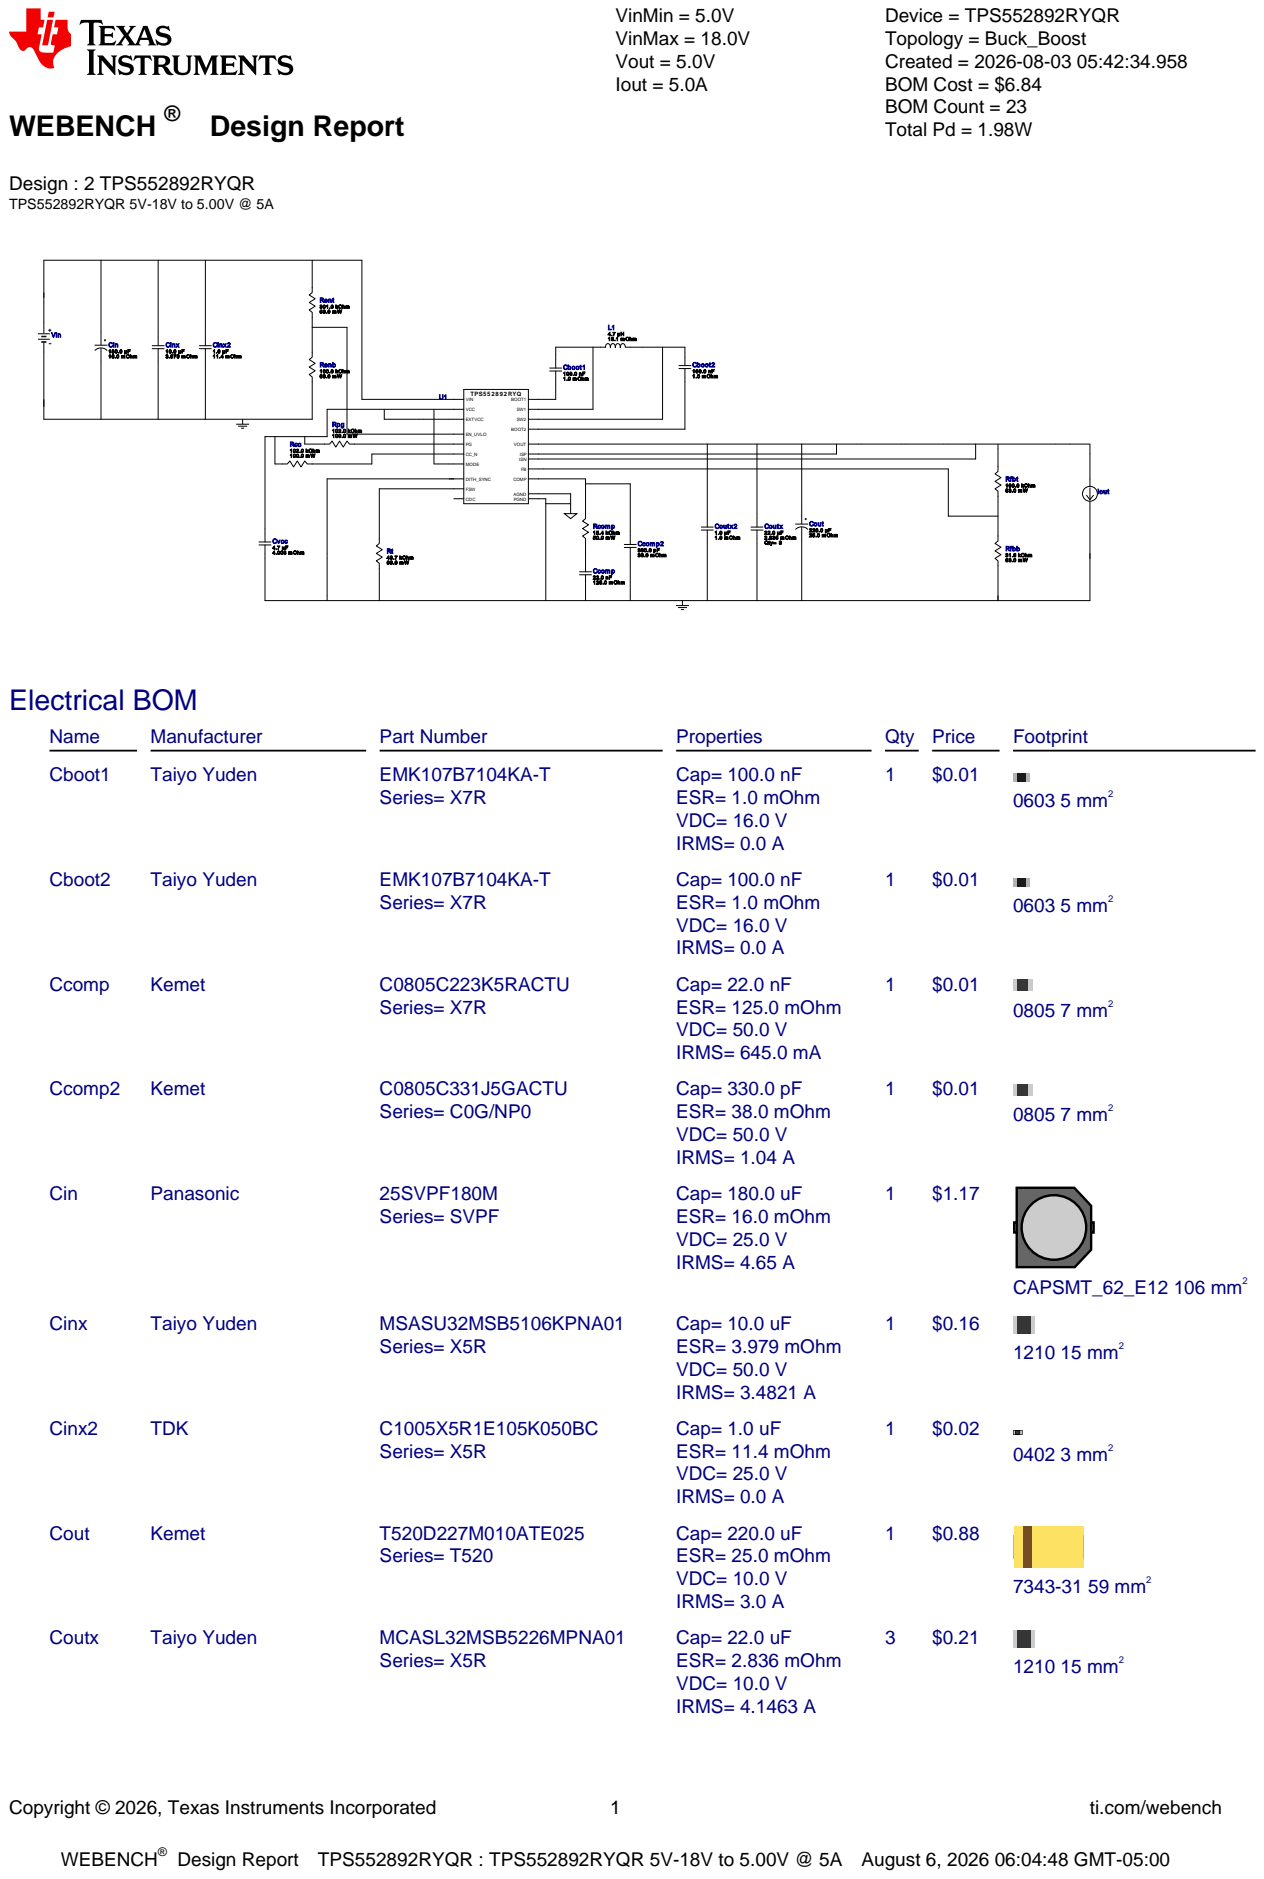
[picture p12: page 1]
Copyright © 2026, Texas Instruments Incorporated; ti.com/webench; WEBENCH®; Design : 2 TPS552892RYQR TPS552892RYQR 5V-18V to 5.00V @ 5A; VinMin = 5.0V VinMax = 18.0V Vout = 5.0V Iout = 5.0A; Device = TPS552892RYQR Topology = Buck_Boost Created = 2026-08-03 05:42:34.958 BOM Cost = $6.84 BOM Count = 23 Total Pd = 1.98W; Ccom p2 330.0 pF 38.0 m Ohm; Rcom p 15.4 kOhm 50.0 m W; Coutx2 1.0 µF 1.0 m Ohm; L1 4.7 µH 13.1 m Ohm Cinx; 3.979 m Ohm Cin 180.0 µF 16.0 m Ohm; Ccom p 22.0 nF 125.0 m Ohm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

Qty= 3 Rt 48.7 kOhm

Design Report TPS552892RYQR : TPS552892RYQR 5V-18V to 5.00V @ 5A August 6, 2026 06:04:48 GMT-05:00

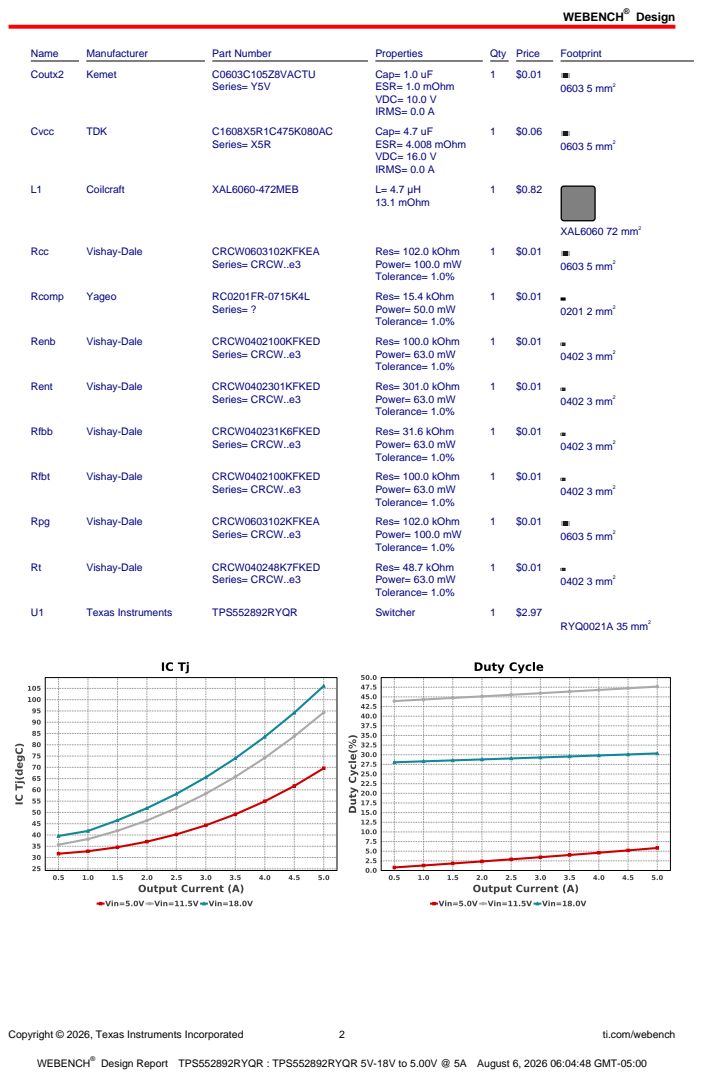
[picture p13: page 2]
Design; Copyright © 2026, Texas Instruments Incorporated; ti.com/webench; Name; Manufacturer; Part Number; Properties; Qty Price; Footprint; Coutx2; Kemet; C0603C105Z8VACTU; Series= Y5V; Cap= 1.0 uF ESR= 1.0 mOhm VDC= 10.0 V IRMS= 0.0 A; 0603 5 mm²; Cvcc; TDK; Series= X5R; Cap= 4.7 uF ESR= 4.008 mOhm VDC= 16.0 V IRMS= 0.0 A; Coilcraft; XAL6060-472MEB; 13.1 mOhm; XAL6060 72 mm²; Rcc; Vishay-Dale; CRCW0603102KFKEA; Series= CRCW..e3; Res= 102.0 kOhm Power= 100.0 mW Tolerance= 1.0%; Rcomp; Yageo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

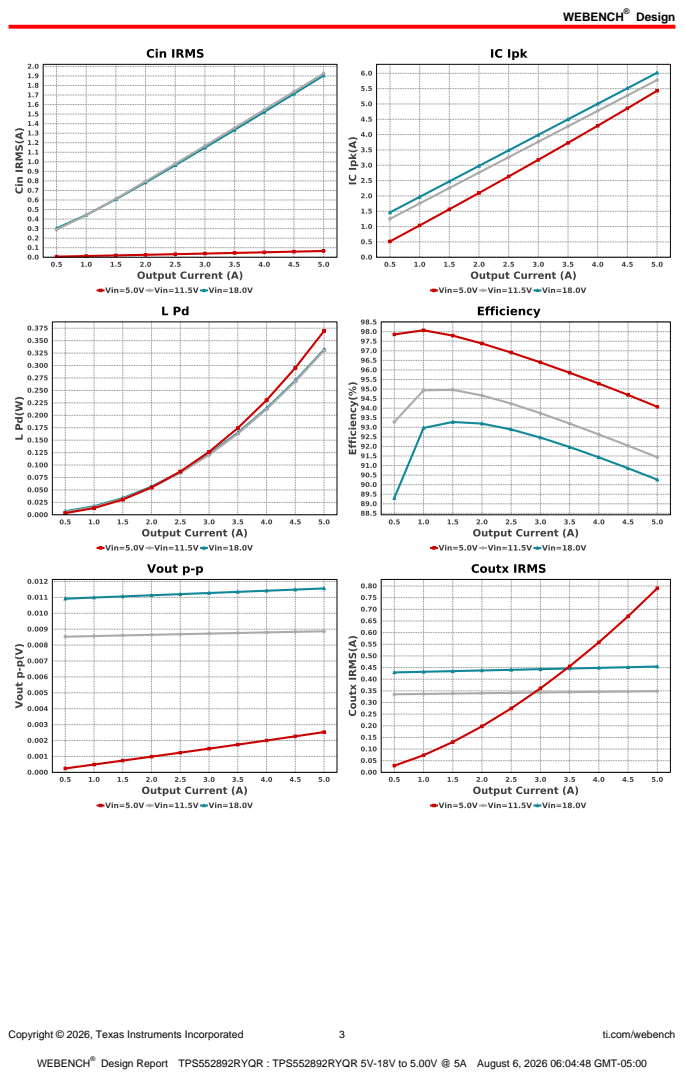
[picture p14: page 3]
Copyright © 2026, Texas Instruments Incorporated; ti.com/webench

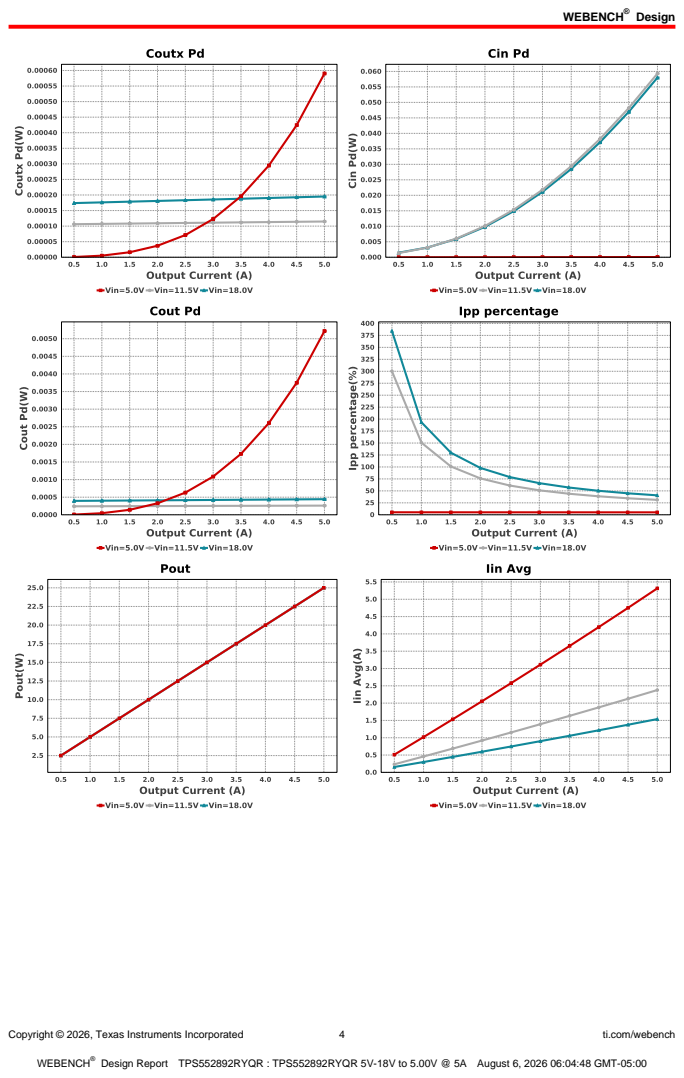
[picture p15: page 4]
Copyright © 2026, Texas Instruments Incorporated; ti.com/webench

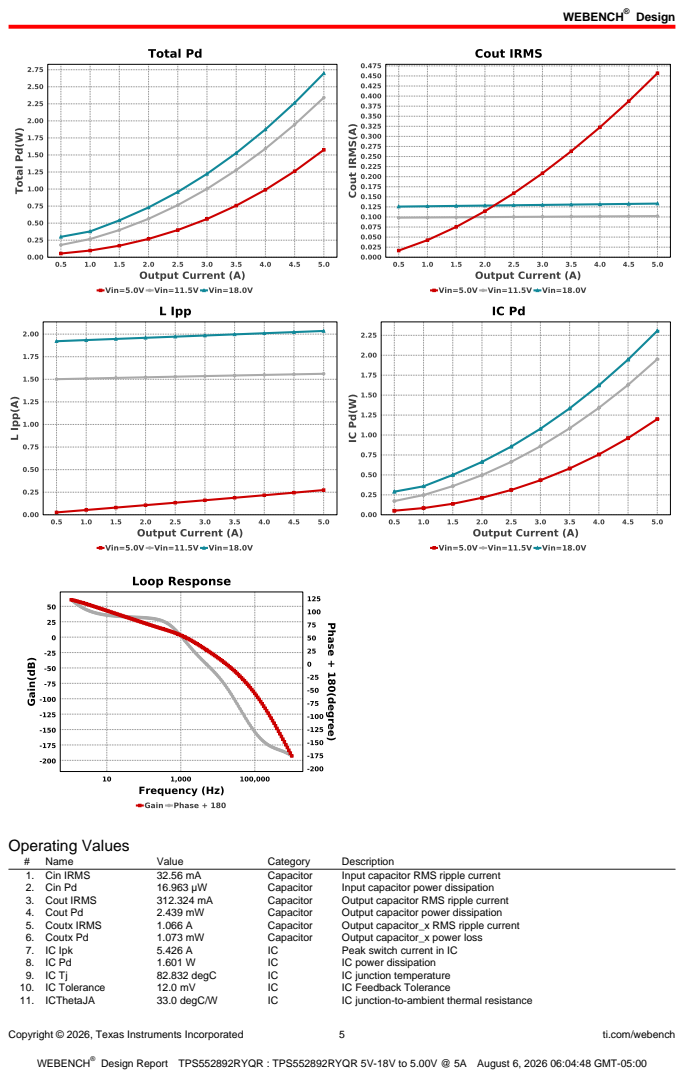
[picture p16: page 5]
Copyright © 2026, Texas Instruments Incorporated; ti.com/webench; Operating Values; Name; Value; Category; Description; 1. Cin IRMS; Capacitor; Input capacitor RMS ripple current; 2. Cin Pd; Input capacitor power dissipation; 3. Cout IRMS; Output capacitor RMS ripple current; 4. Cout Pd; Output capacitor power dissipation; 5. Coutx IRMS; Output capacitor_x RMS ripple current; 6. Coutx Pd; Output capacitor_x power loss; 7. IC Ipk; Peak switch current in IC; IC power dissipation; 82.832 degC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

Copyright © 2026, Texas Instruments Incorporated | 6 | ti.com/webench
# | Name | Value | Category | Description

12. Iin Avg | 5.397 A | IC | Average input current
13. Ipp percentage | 2.935 % | Inductor | Inductor ripple current percentage (with respect to average inductor
| | | | current)
14. L Ipp | 157.88 mA | Inductor | Peak-to-peak inductor ripple current
15. L Pd | 379.1 mW | Inductor | Inductor power dissipation
16. Cin Pd | 16.963 µW | Power | Input capacitor power dissipation
17. Cout Pd | 2.439 mW | Power | Output capacitor power dissipation
18. Coutx Pd | 1.073 mW | Power | Output capacitor_x power loss
19. IC Pd | 1.601 W | Power | IC power dissipation
20. L Pd | 379.1 mW | Power | Inductor power dissipation
21. Total Pd | 1.984 W | Power | Total Power Dissipation
22. BOM Count | 23 | System
| | | Information | Total Design BOM count
23. Cross Freq | 1.681 kHz | System
| | | Information | Bode plot crossover frequency
24. Duty Cycle | 7.051 % | System
| | | Information | Duty cycle
25. Efficiency | 92.648 % | System
| | | Information | Steady state efficiency
26. FootPrint | 392.0 mm² | System
| | | Information | Total Foot Print Area of BOM components
27. Frequency | 402.82 kHz | System
| | | Information | Switching frequency
28. Gain Marg | -24.837 dB | System
| | | Information | Bode Plot Gain Margin
29. Iout | 5.0 A | System
| | | Information | Iout operating point
30. Low Freq Gain | 54.683 dB | System
| | | Information | Gain at 1Hz
31. Mode | CCM | System
| | | Information | Conduction Mode
32. Phase Marg | 102.68 deg | System
| | | Information | Bode Plot Phase Margin
33. Pout | 25.0 W | System
| | | Information | Total output power
34. Total BOM | $6.84 | System
| | | Information | Total BOM Cost
35. Vin | 5.0 V | System
| | | Information | Vin operating point
36. Vout | 5.0 V | System
| | | Information | Operational Output Voltage
37. Vout Actual | 4.997 V | System
| | | Information | Vout Actual calculated based on selected voltage divider resistors
38. Vout Tolerance | 2.55 % | System
| | | Information | Vout Tolerance based on IC Tolerance (no load) and voltage divider resistors if applicable
39. Vout p-p | 897.007 µV | System
| | | Information | Peak-to-peak output ripple voltage
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

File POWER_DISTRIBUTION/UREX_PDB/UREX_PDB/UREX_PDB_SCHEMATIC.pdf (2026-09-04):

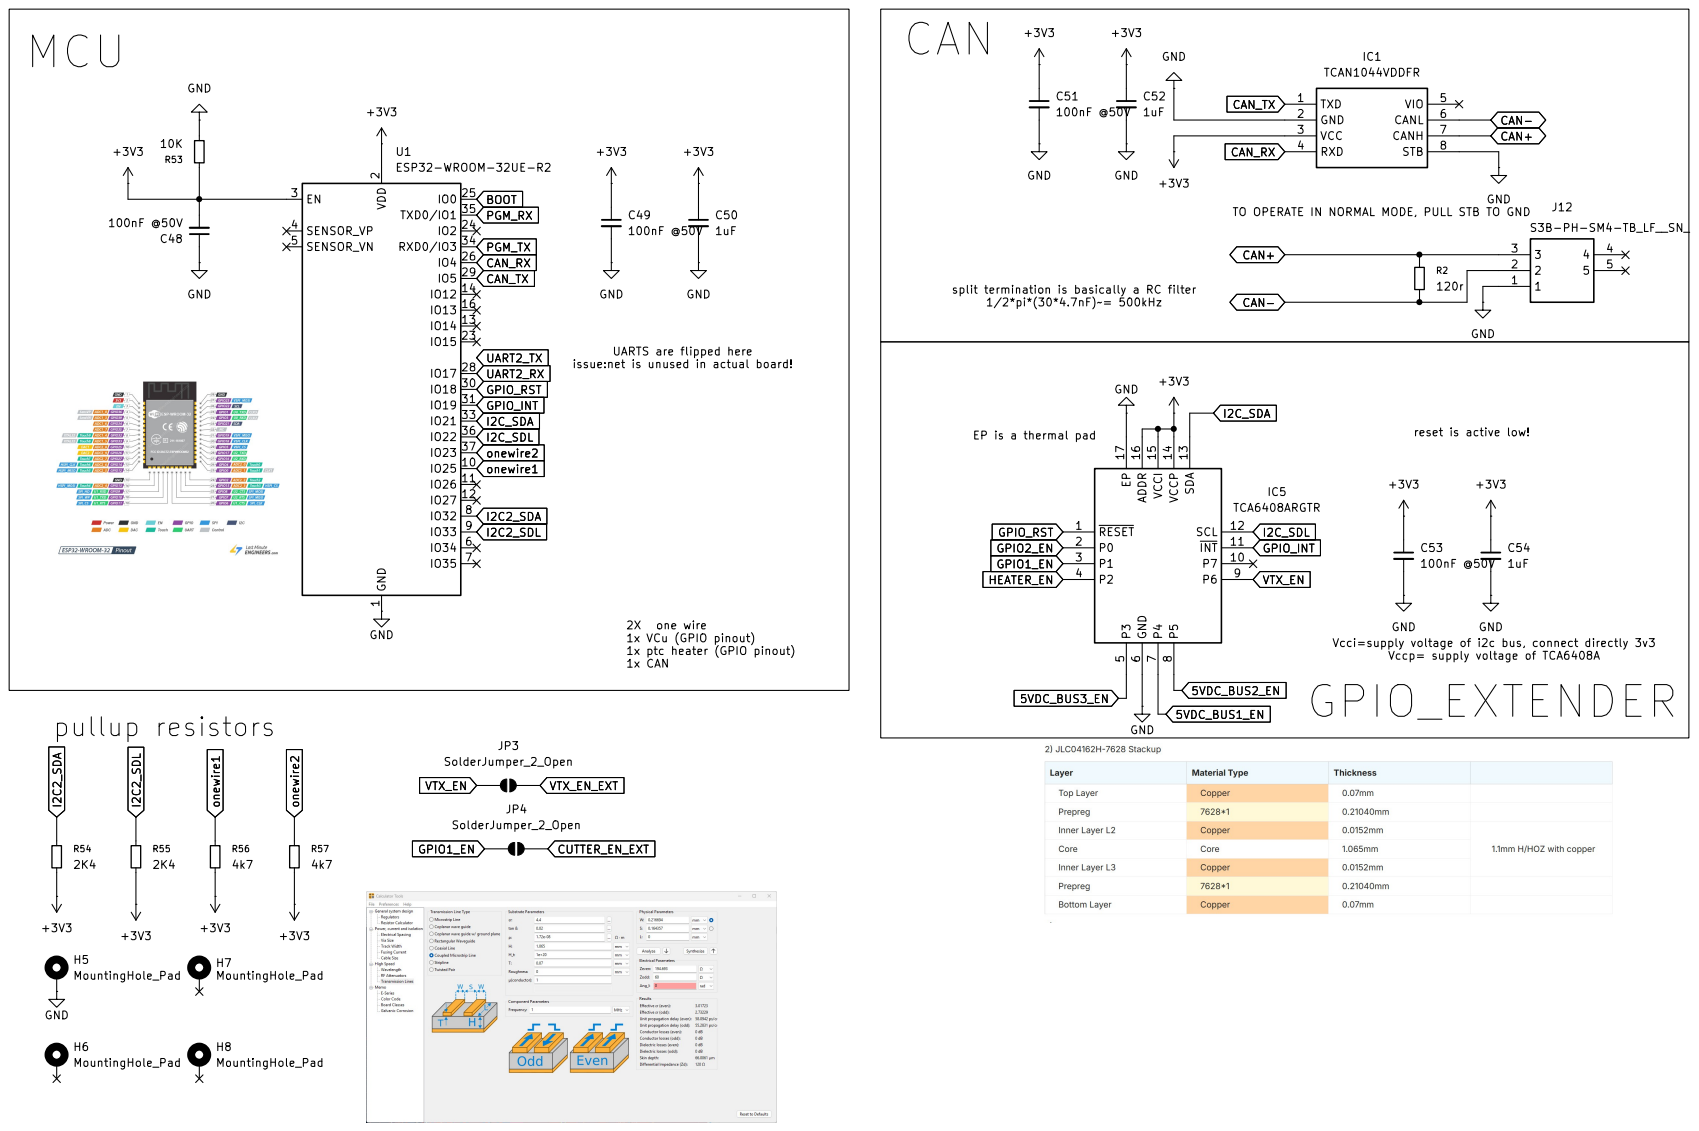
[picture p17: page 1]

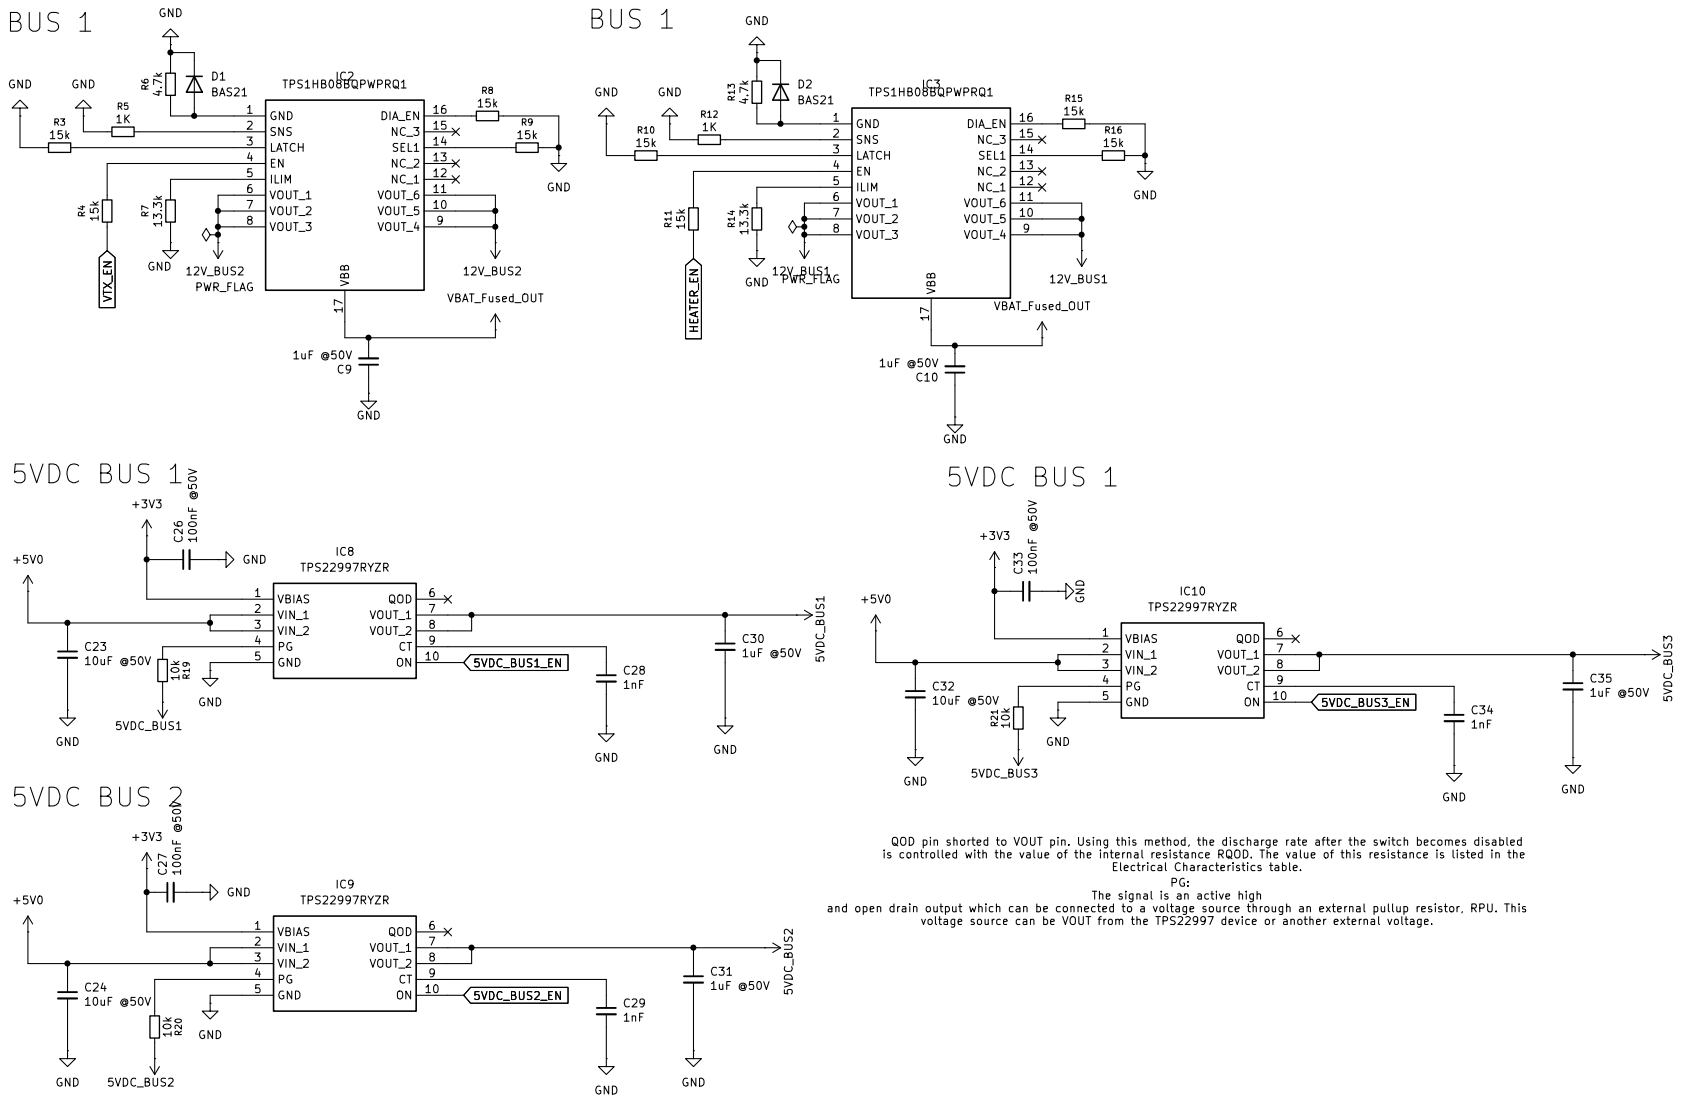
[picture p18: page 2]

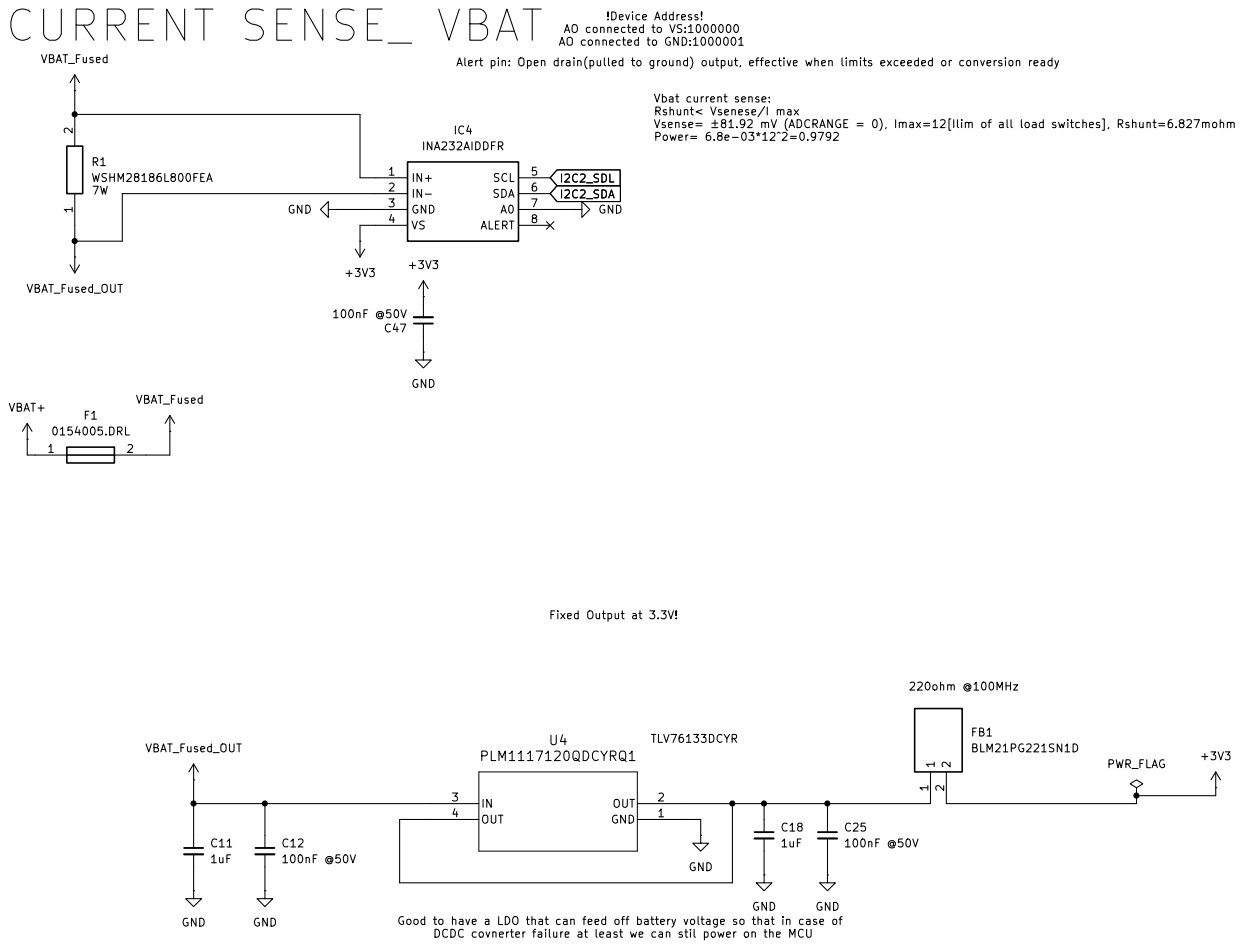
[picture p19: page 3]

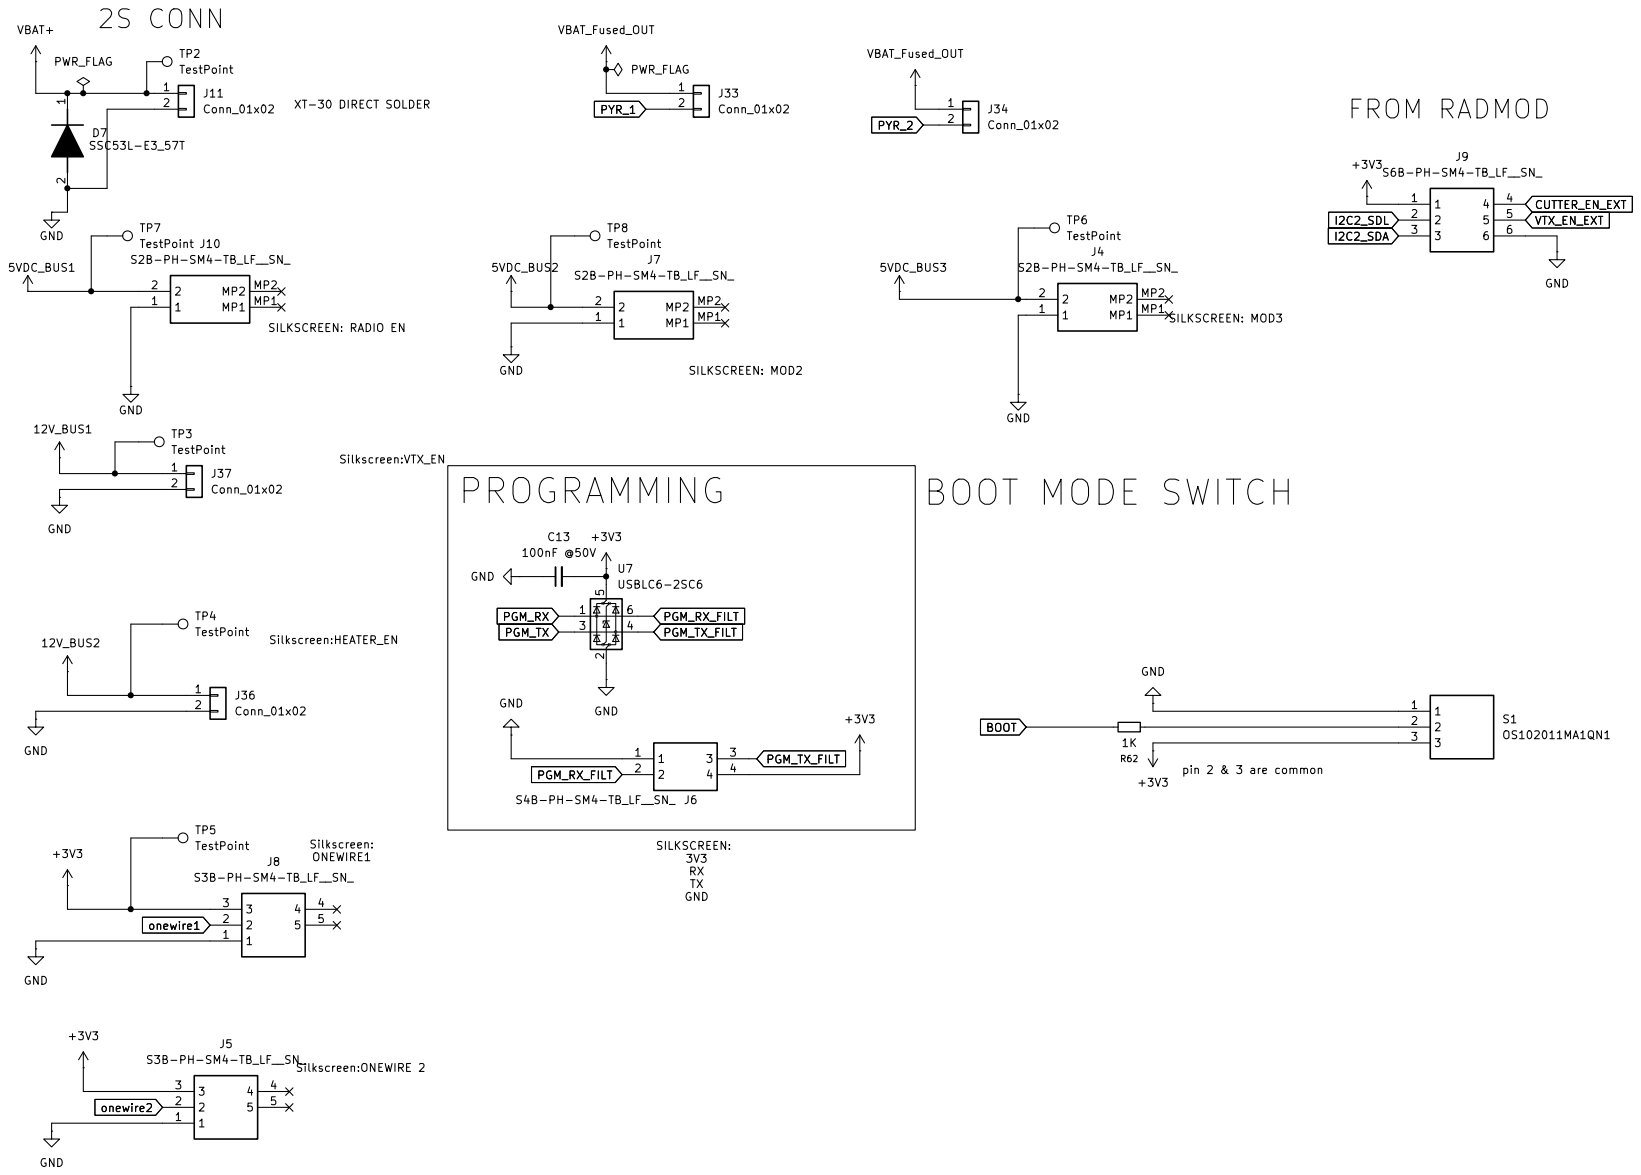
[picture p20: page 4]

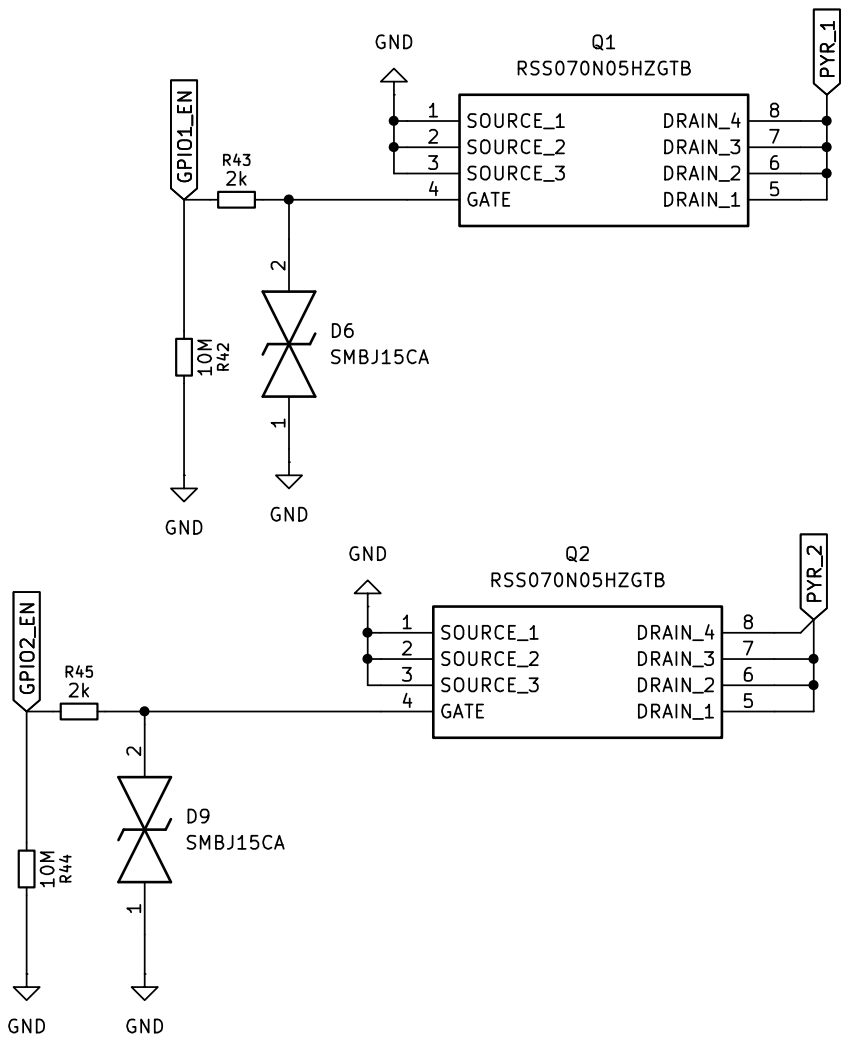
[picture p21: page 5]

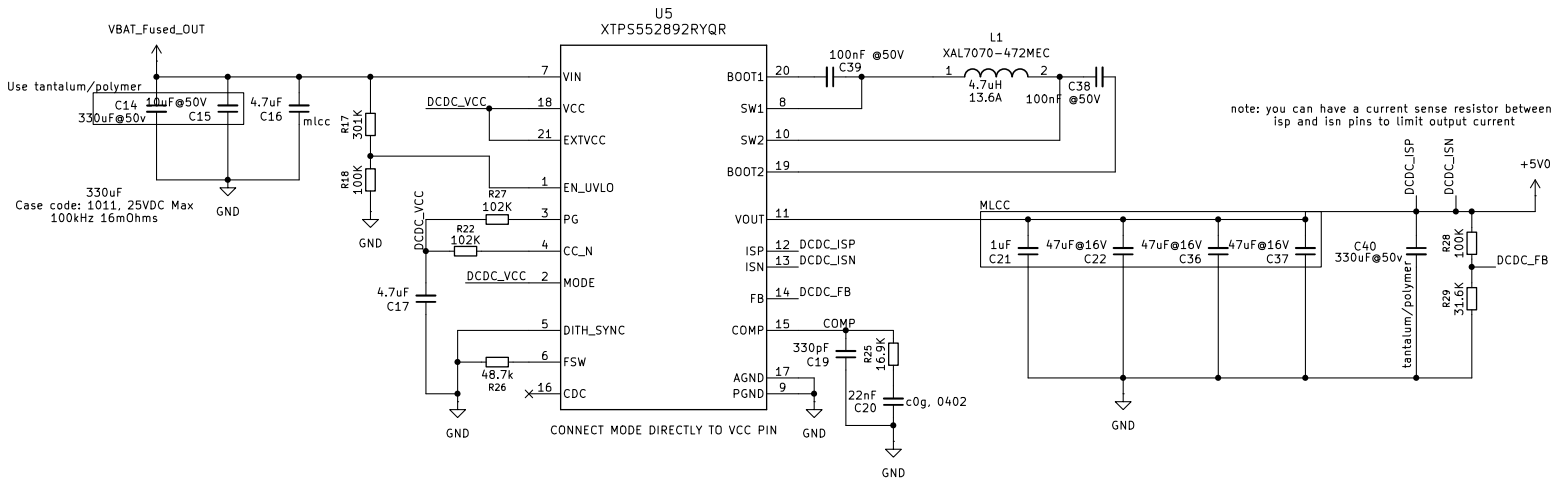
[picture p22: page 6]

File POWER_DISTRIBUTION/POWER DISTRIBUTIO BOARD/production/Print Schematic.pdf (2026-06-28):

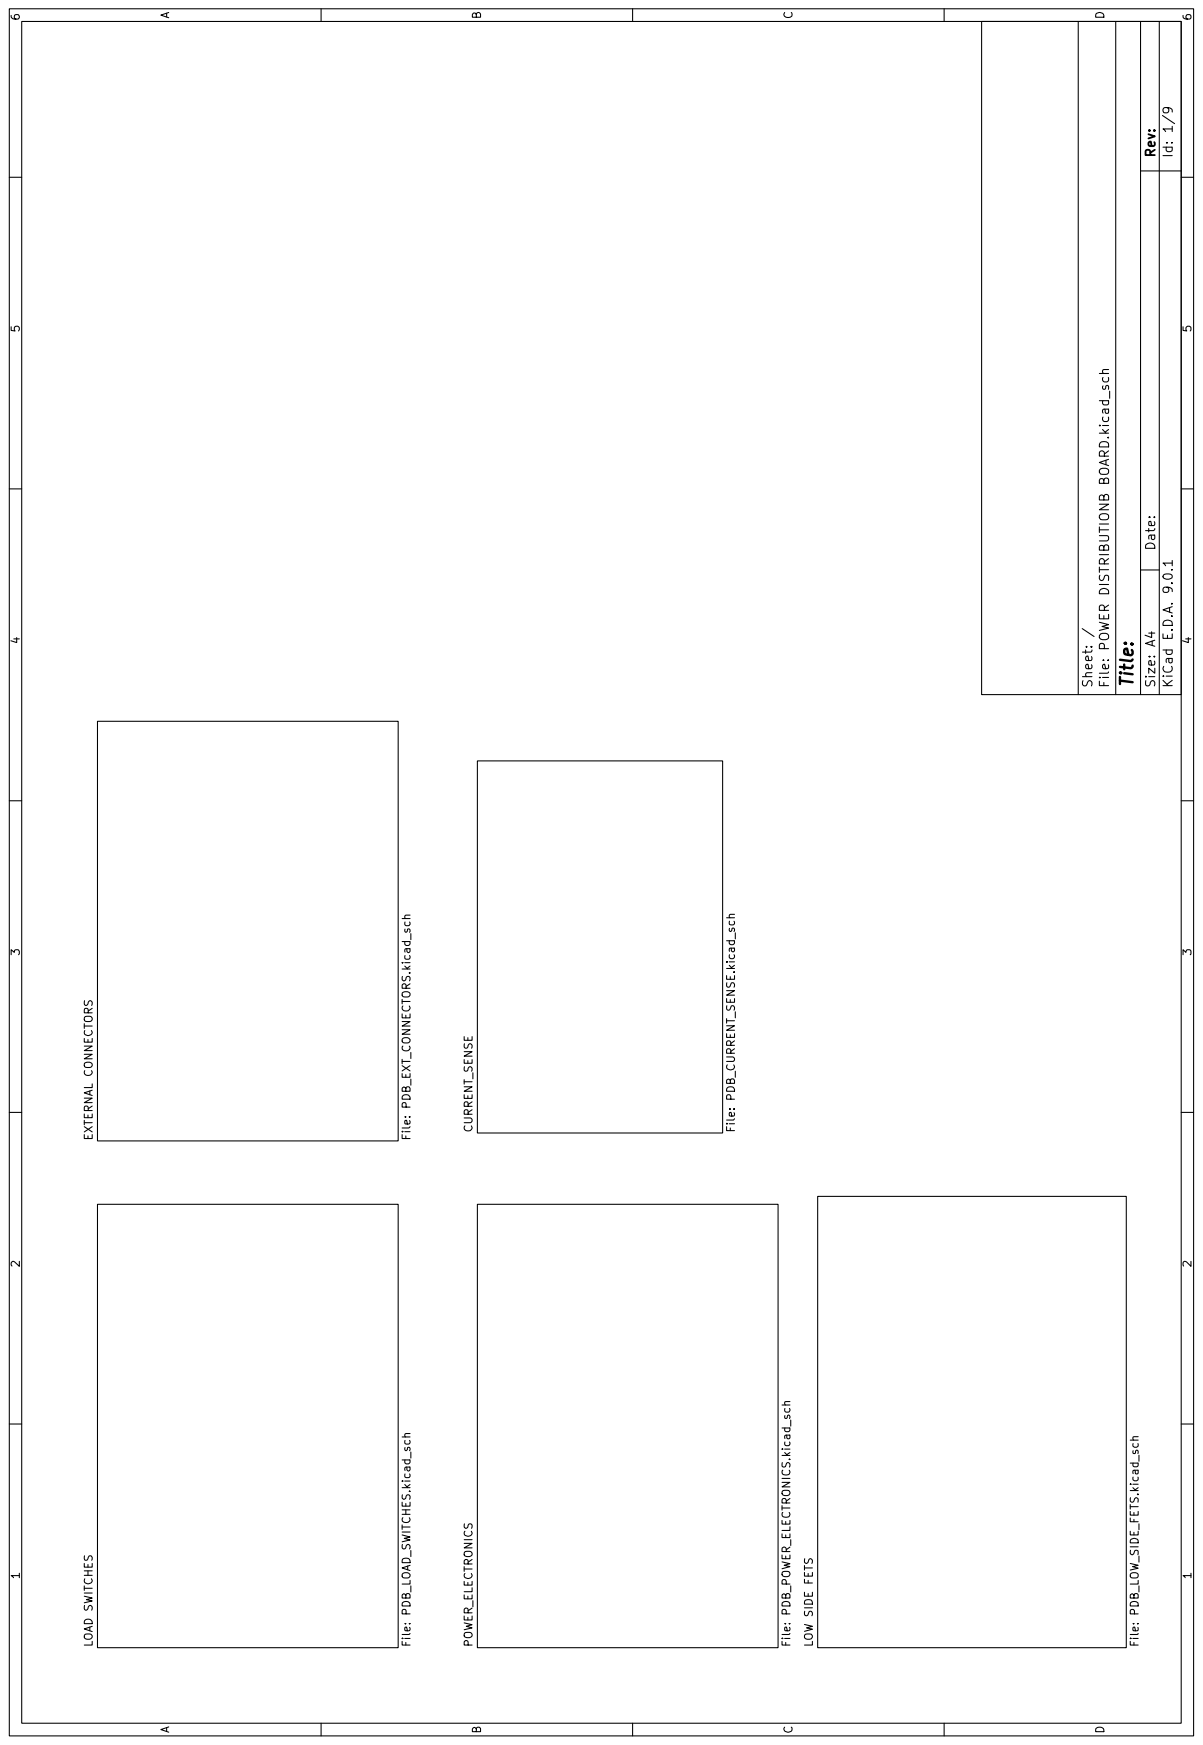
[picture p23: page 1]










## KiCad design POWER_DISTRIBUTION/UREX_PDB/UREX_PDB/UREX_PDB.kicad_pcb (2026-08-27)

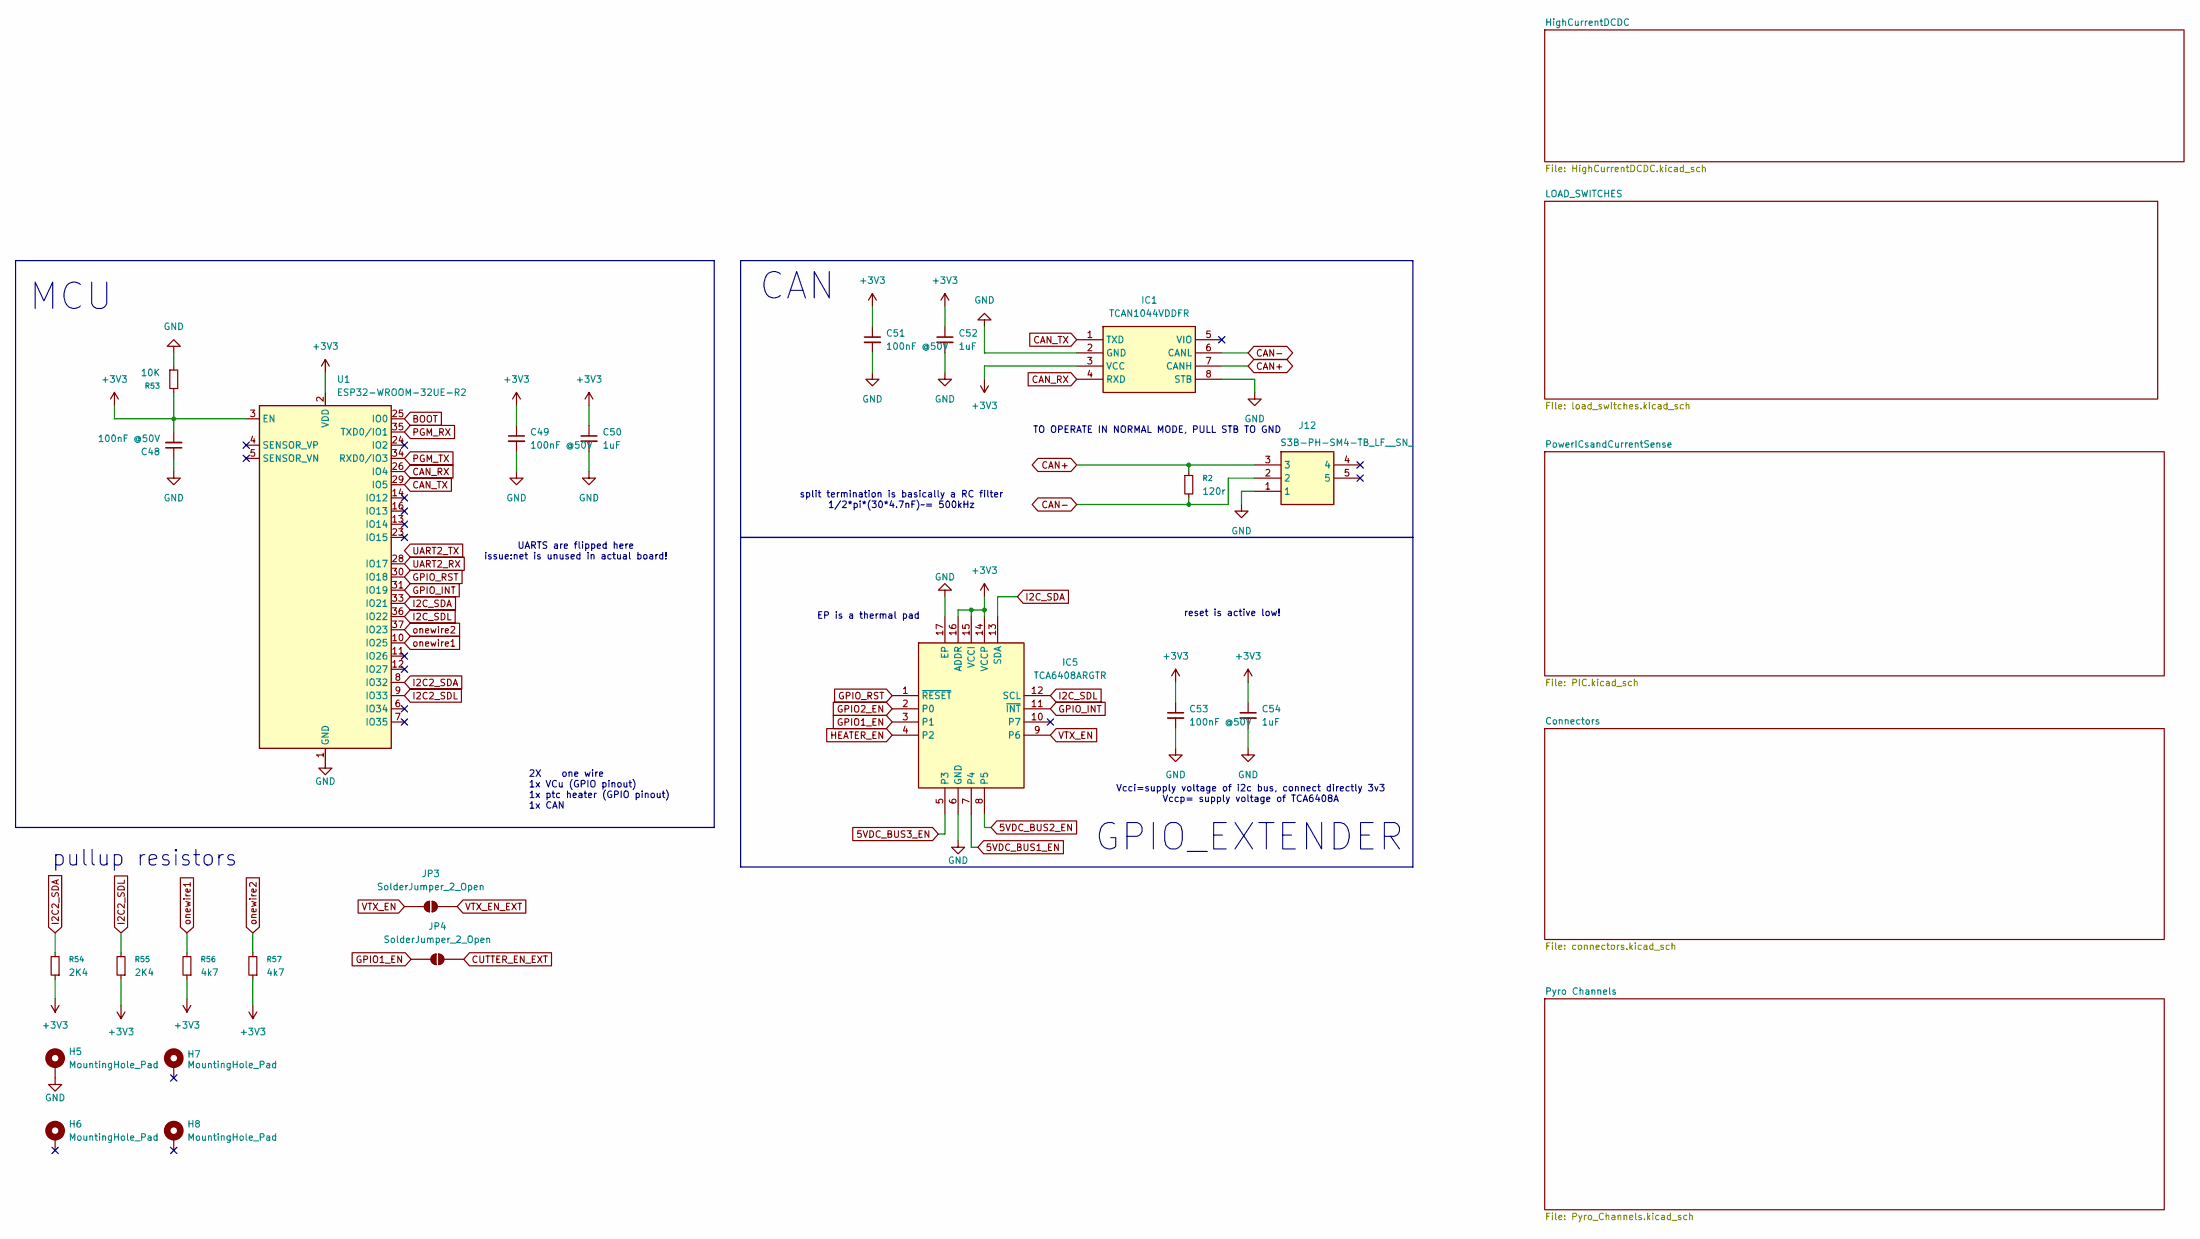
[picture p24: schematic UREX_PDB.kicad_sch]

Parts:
C48, C49, C51, C53: 100nF @50V; C_0603_1608Metric
C50, C52, C54: 1uF; C_0603_1608Metric
H5, H7, H8: MountingHole_Pad; MountingHole_2.2mm_M2_ISO7380
H6: MountingHole_Pad; MountingHole_2.2mm_M2_Pad_Via
IC1: TCAN1044VDDFR; SOT65P280X110-8N; Mouser Part Number 595-TCAN1044VDDFR
IC5: TCA6408ARGTR; QFN50P300X300X100-17N-D; Mouser Part Number 595-TCA6408ARGTR
J12: S3B-PH-SM4-TB_LF__SN_; S3BPHSM4TBLFSN; Mouser Part Number N/A
JP3, JP4: SolderJumper_2_Open; SolderJumper-2_P1.3mm_Open_Pad1.0x1.5mm
R2: 120r; R_0603_1608Metric
R53: 10K; R_0603_1608Metric
R54, R55: 2K4; R_0603_1608Metric
R56, R57: 4k7; R_0603_1608Metric
U1: ESP32-WROOM-32UE-R2; ESP32-WROOM-32UE

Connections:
5VDC_BUS1_EN: IC5.7 (P4); also elsewhere on the board
5VDC_BUS2_EN: IC5.8 (P5); also elsewhere on the board
5VDC_BUS3_EN: IC5.5 (P3); also elsewhere on the board
+3V3: C48.2, C49.1, C50.1, C51.1, C52.1, C53.1, C54.1, IC1.3 (VCC), IC5.14 (VCCP), IC5.15 (VCCI), IC5.16 (ADDR), R53.2, R54.1, R55.1, R56.1, R57.1, U1.2 (VDD), U1.3 (EN); also elsewhere on the board
BOOT: U1.25 (IO0); also elsewhere on the board
CAN+: IC1.7 (CANH), J12.3, R2.1
CAN-: IC1.6 (CANL), J12.2, R2.2
CAN_RX: IC1.4 (RXD), U1.26 (IO4)
CAN_TX: IC1.1 (TXD), U1.29 (IO5)
CUTTER_EN_EXT: JP4.2 (B); also elsewhere on the board
GND: C48.1, C49.2, C50.2, C51.2, C52.2, C53.2, C54.2, H5.1, IC1.2 (GND), IC1.8 (STB), IC5.6 (GND), IC5.17 (EP), J12.1, R53.1, U1.1 (GND), U1.15 (GND), U1.38 (GND), U1.39 (GND); also elsewhere on the board
GPIO1_EN: IC5.3 (P1), JP4.1 (A); also elsewhere on the board
GPIO2_EN: IC5.2 (P0); also elsewhere on the board
GPIO_INT: IC5.11 (~INT), U1.31 (IO19)
GPIO_RST: IC5.1 (~RESET), U1.30 (IO18)
HEATER_EN: IC5.4 (P2); also elsewhere on the board
I2C2_SDA: R54.2, U1.8 (IO32); also elsewhere on the board
I2C2_SDL: R55.2, U1.9 (IO33); also elsewhere on the board
I2C_SDA: IC5.13 (SDA), U1.33 (IO21)
I2C_SDL: IC5.12 (SCL), U1.36 (IO22)
PGM_RX: U1.35 (TXD0/IO1); also elsewhere on the board
PGM_TX: U1.34 (RXD0/IO3); also elsewhere on the board
UART2_RX: U1.28 (IO17)
VTX_EN: IC5.9 (P6), JP3.1 (A); also elsewhere on the board
VTX_EN_EXT: JP3.2 (B); also elsewhere on the board
onewire1: R56.2, U1.10 (IO25); also elsewhere on the board
onewire2: R57.2, U1.37 (IO23); also elsewhere on the board

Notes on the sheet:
UARTS are flipped here issue:net is unused in actual board!
TO OPERATE IN NORMAL MODE, PULL STB TO GND
reset is active low!
pullup resistors
Vcci=supply voltage of i2c bus, connect directly 3v3 Vccp= supply voltage of TCA6408A
MCU
EP is a thermal pad
2X one wire 1x VCu (GPIO pinout) 1x ptc heater (GPIO pinout) 1x CAN
GPIO_EXTENDER
split termination is basically a RC filter 1/2*pi*(30*4.7nF)~= 500kHz
CAN

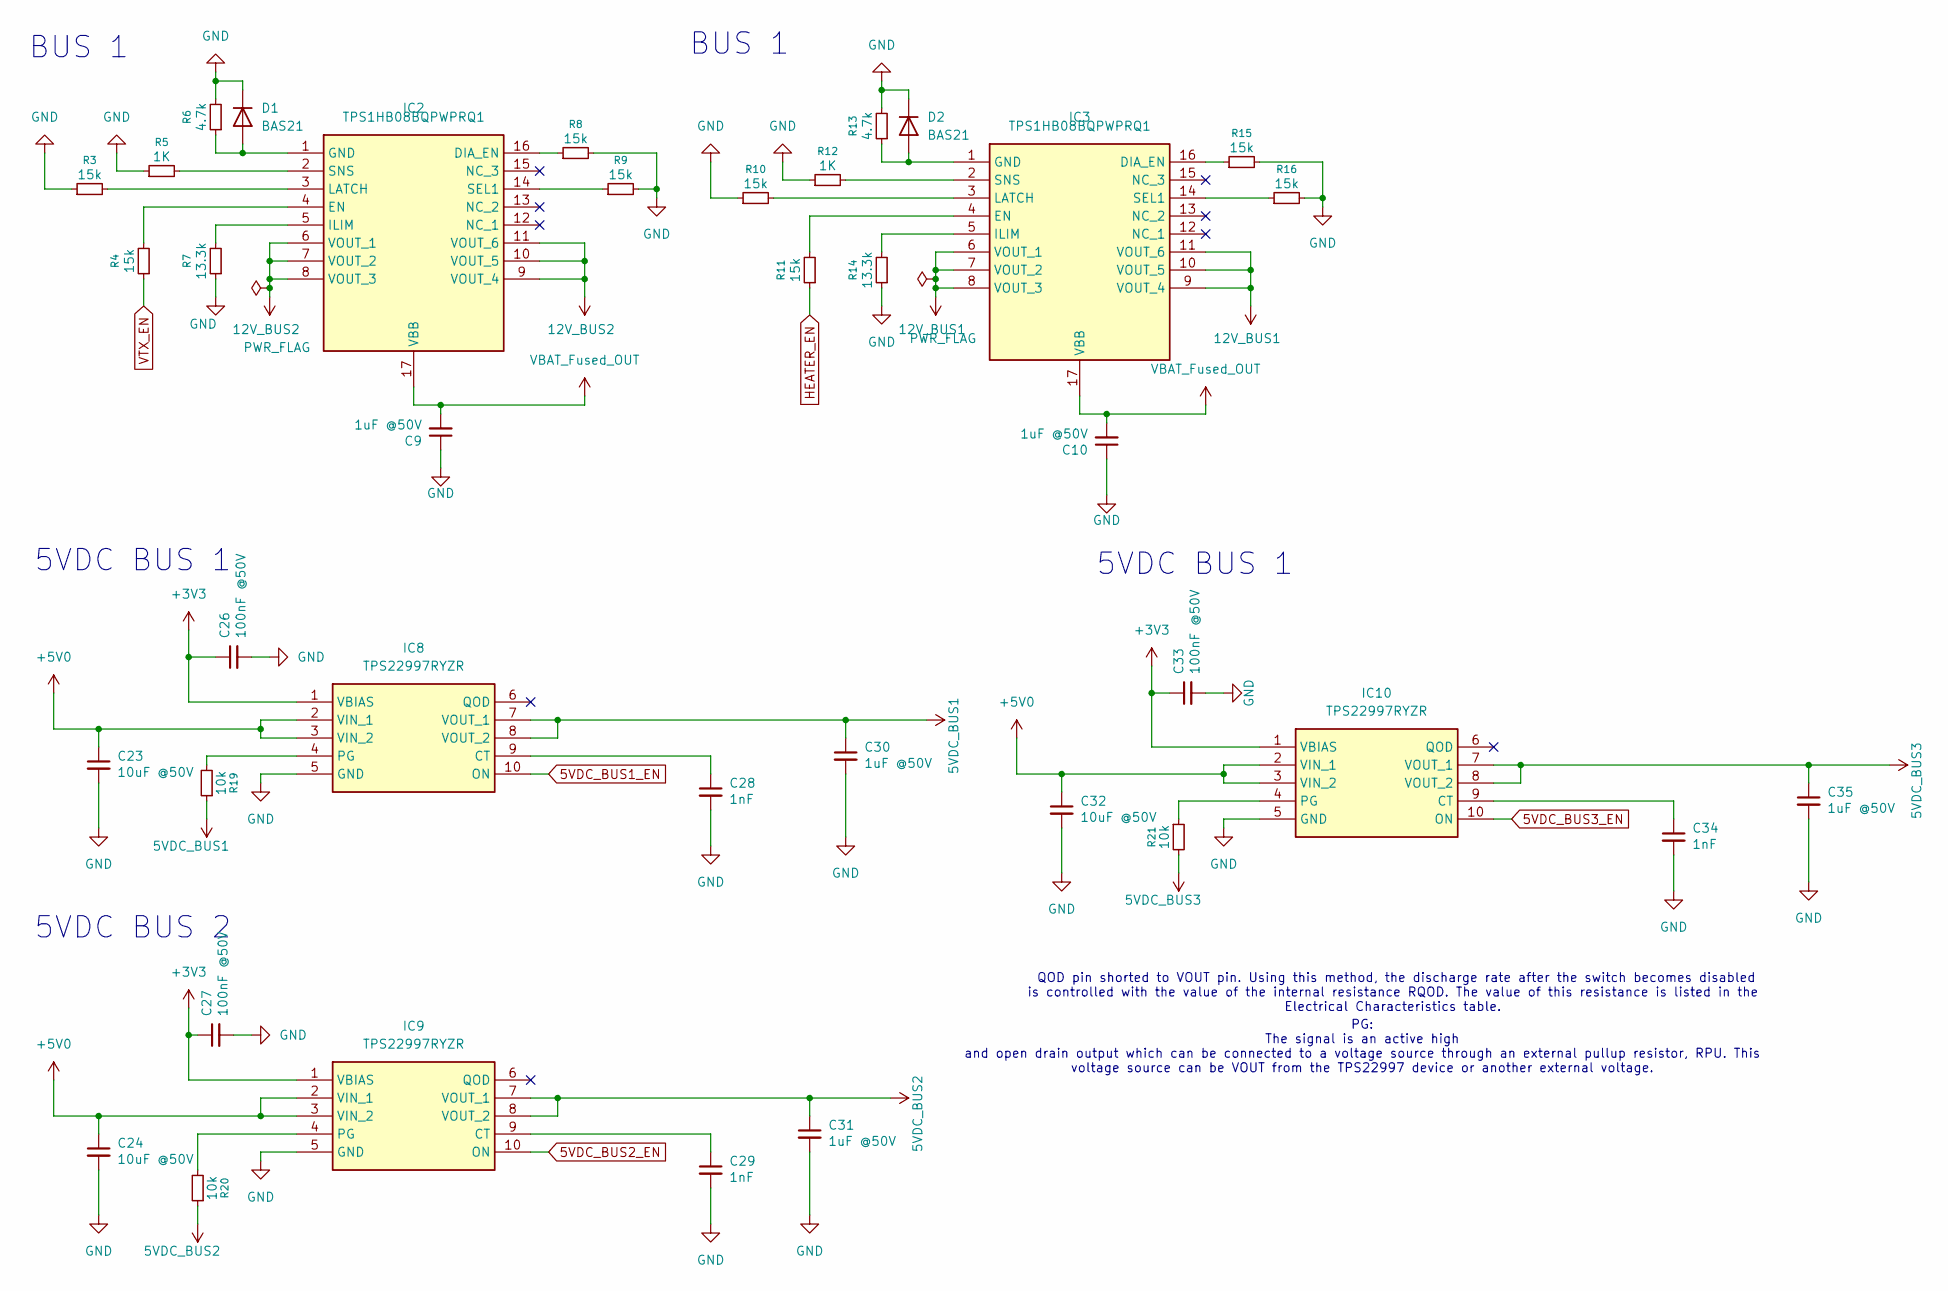
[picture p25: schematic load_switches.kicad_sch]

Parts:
C9, C10: 1uF @50V; C_0805_2012Metric_Pad1.18x1.45mm_HandSolder
C23, C24: 10uF @50V; C_1210_3225Metric_Pad1.33x2.70mm_HandSolder; Manufacturer_Part_Number GRM32EC72A106KE05L
C26, C27, C33: 100nF @50V; C_0402_1005Metric_Pad0.74x0.62mm_HandSolder
C28, C29, C34: 1nF; C_0603_1608Metric
C30, C31, C35: 1uF @50V; C_0805_2012Metric
C32: 10uF @50V; C_1210_3225Metric; Manufacturer_Part_Number GRM32EC72A106KE05L
D1, D2: BAS21; SOT-23
IC2, IC3: TPS1HB08BQPWPRQ1; SOP65P640X120-17N; Mouser Part Number 595-TPS1HB08BQPWPRQ1
IC8, IC9, IC10: TPS22997RYZR; Mouser Part Number 595-TPS22997RYZR
R3, R4, R8, R9, R10, R11, R15, R16: 15k; R_0603_1608Metric
R5, R12: 1K; R_0603_1608Metric
R6, R13: 4.7k; R_0603_1608Metric
R7, R14: 13.3k; R_0603_1608Metric
R19, R20, R21: 10k; R_0402_1005Metric_Pad0.72x0.64mm_HandSolder

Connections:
5VDC_BUS1: C30.1, IC8.7 (VOUT_1), IC8.8 (VOUT_2), R19.1; also elsewhere on the board
5VDC_BUS1_EN: IC8.10 (ON); also elsewhere on the board
5VDC_BUS2: C31.1, IC9.7 (VOUT_1), IC9.8 (VOUT_2), R20.1; also elsewhere on the board
5VDC_BUS2_EN: IC9.10 (ON); also elsewhere on the board
5VDC_BUS3: C35.1, IC10.7 (VOUT_1), IC10.8 (VOUT_2), R21.2; also elsewhere on the board
5VDC_BUS3_EN: IC10.10 (ON); also elsewhere on the board
12V_BUS1: IC3.6 (VOUT_1), IC3.7 (VOUT_2), IC3.8 (VOUT_3), IC3.9 (VOUT_4), IC3.10 (VOUT_5), IC3.11 (VOUT_6); also elsewhere on the board
12V_BUS2: IC2.6 (VOUT_1), IC2.7 (VOUT_2), IC2.8 (VOUT_3), IC2.9 (VOUT_4), IC2.10 (VOUT_5), IC2.11 (VOUT_6); also elsewhere on the board
+3V3: C26.1, C27.1, C33.1, IC8.1 (VBIAS), IC9.1 (VBIAS), IC10.1 (VBIAS); also elsewhere on the board
+5V0: C23.1, C24.1, C32.1, IC8.2 (VIN_1), IC8.3 (VIN_2), IC9.2 (VIN_1), IC9.3 (VIN_2), IC10.2 (VIN_1), IC10.3 (VIN_2); also elsewhere on the board
GND: C9.1, C10.1, C23.2, C24.2, C26.2, C27.2, C28.2, C29.2, C30.2, C31.2, C32.2, C33.2, C34.2, C35.2, D1.3 (K), D2.3 (K), IC8.5 (GND), IC9.5 (GND), IC10.5 (GND), R3.1, R5.1, R6.2, R7.1, R8.2, R9.2, R10.1, R12.1, R13.2, R14.1, R15.2, R16.2; also elsewhere on the board
HEATER_EN: R11.1; also elsewhere on the board
unnamed: D1.1 (A), IC2.1 (GND), R6.1
unnamed: D2.1 (A), IC3.1 (GND), R13.1
unnamed: IC2.16 (DIA_EN), R8.1
unnamed: IC2.4 (EN), R4.2
unnamed: IC2.5 (ILIM), R7.2
unnamed: IC2.3 (LATCH), R3.2
unnamed: IC2.14 (SEL1), R9.1
unnamed: IC2.2 (SNS), R5.2
unnamed: IC3.16 (DIA_EN), R15.1
unnamed: IC3.4 (EN), R11.2
unnamed: IC3.5 (ILIM), R14.2
unnamed: IC3.3 (LATCH), R10.2
unnamed: IC3.14 (SEL1), R16.1
unnamed: IC3.2 (SNS), R12.2
unnamed: C28.1, IC8.9 (CT)
unnamed: IC8.4 (PG), R19.2
unnamed: C29.1, IC9.9 (CT)
unnamed: IC9.4 (PG), R20.2
unnamed: C34.1, IC10.9 (CT)
unnamed: IC10.4 (PG), R21.1
VBAT_Fused_OUT: C9.2, C10.2, IC2.17 (VBB), IC3.17 (VBB); also elsewhere on the board
VTX_EN: R4.1; also elsewhere on the board

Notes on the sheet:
5VDC BUS 2
BUS 1
5VDC BUS 1
PG: The signal is an active high and open drain output which can be connected to a voltage source through an external pullup resistor, RPU. This voltage source can be VOUT from the TPS22997 device or another external voltage.
QOD pin shorted to VOUT pin. Using this method, the discharge rate after the switch becomes disabled is controlled with the value of the internal resistance RQOD. The value of this resistance is listed in the Electrical Characteristics table.

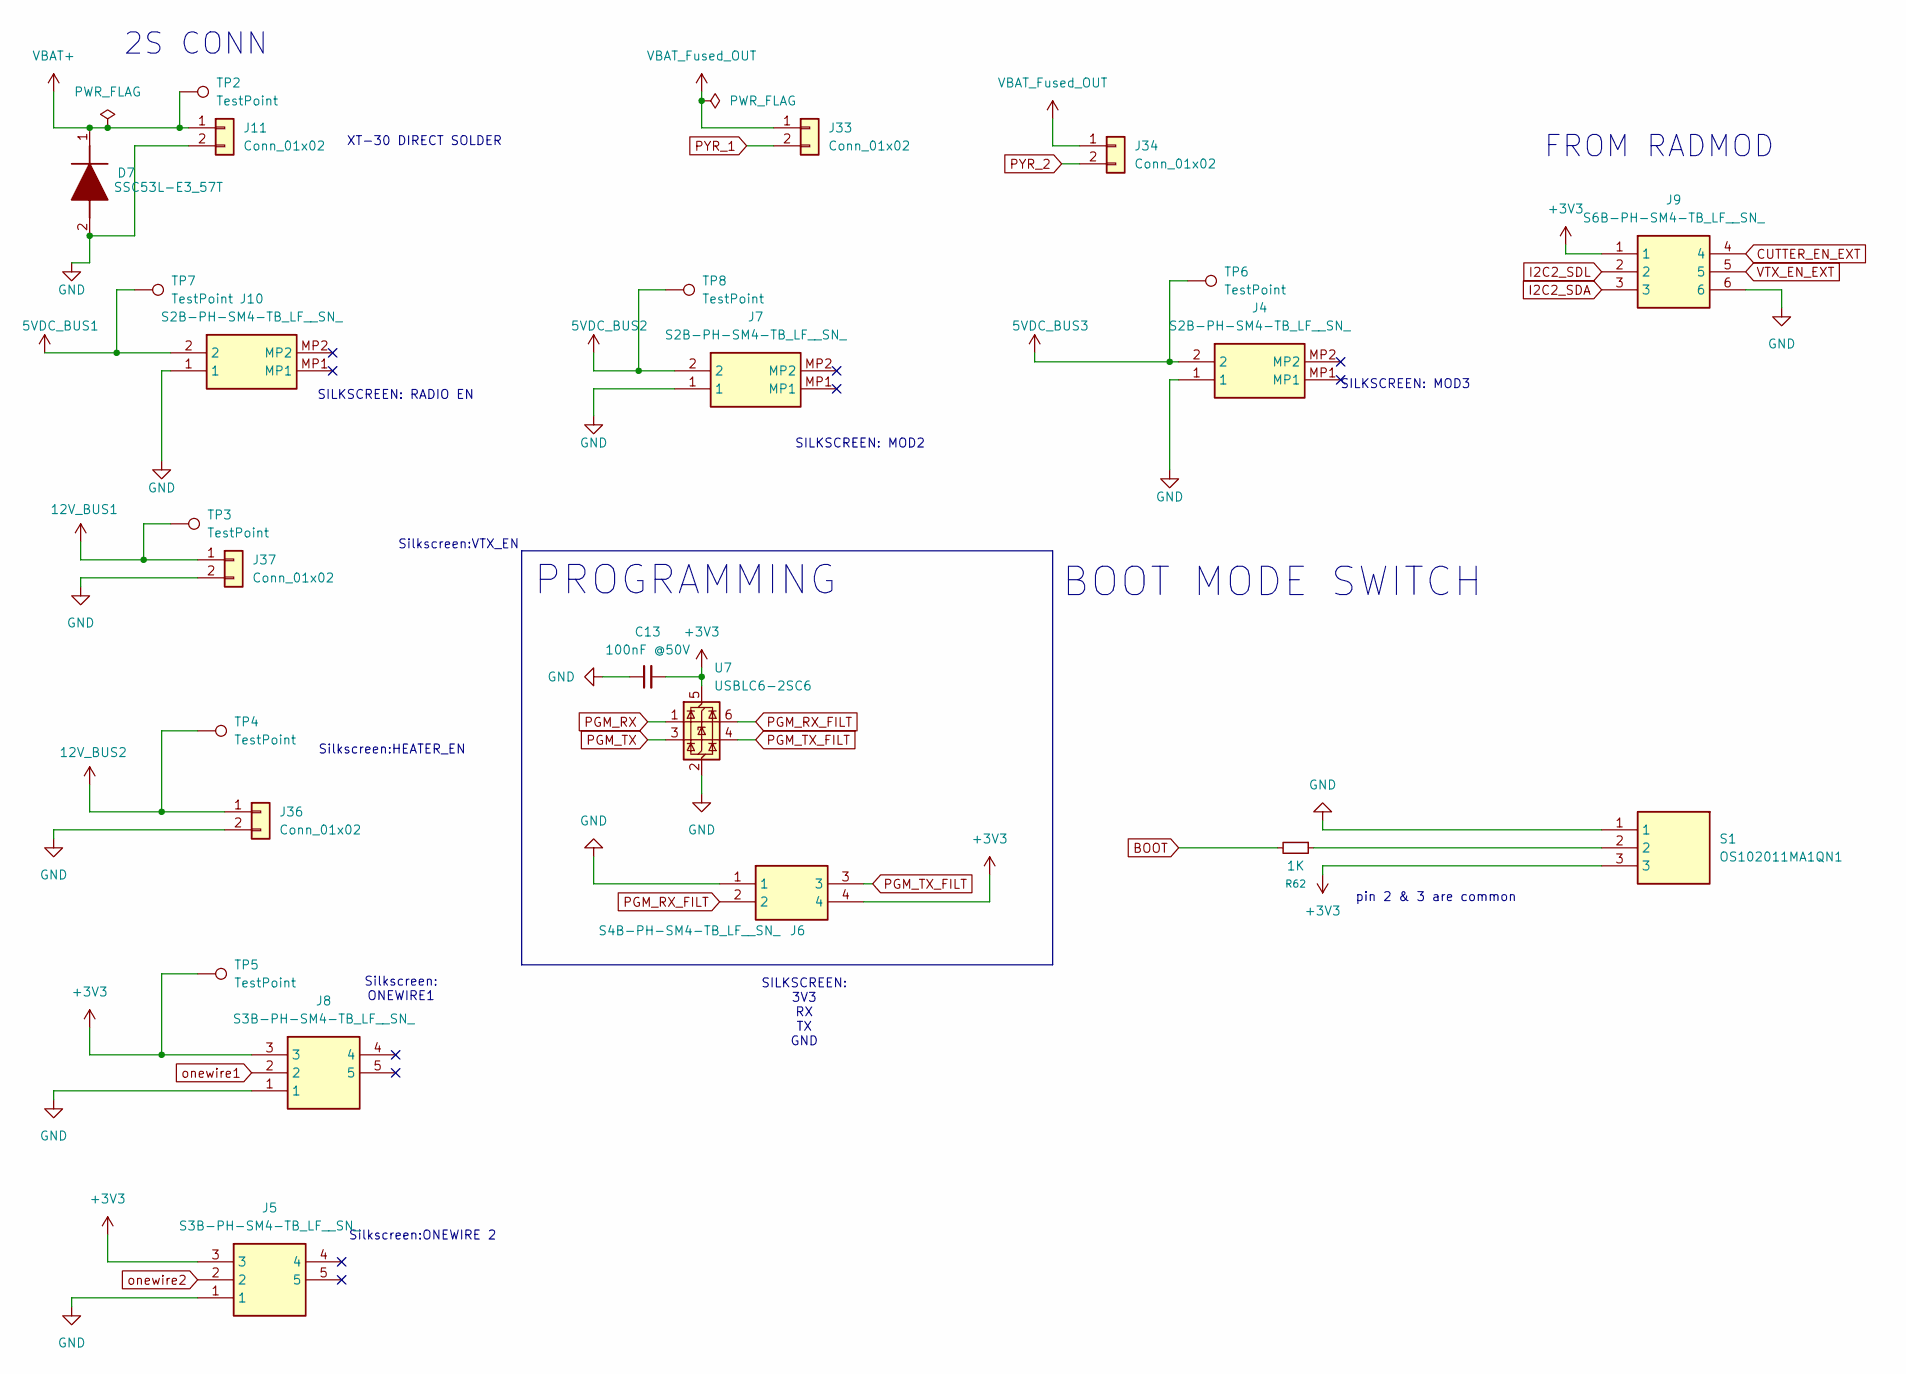
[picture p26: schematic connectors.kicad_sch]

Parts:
C13: 100nF @50V; C_0603_1608Metric
D7: SSC53L-E3_57T; DIOM7959X262N; Manufacturer_Part_Number SSC53L-E3/57T; Mouser Part Number 625-SSC53L-E3
J4, J7, J10: S2B-PH-SM4-TB_LF__SN_; S2BPHSM4TBLFSN; Mouser Part Number N/A
J5, J8: S3B-PH-SM4-TB_LF__SN_; S3BPHSM4TBLFSN; Mouser Part Number N/A
J6: S4B-PH-SM4-TB_LF__SN_; S4B-PH-SM4-TB; Mouser Part Number N/A
J9: S6B-PH-SM4-TB_LF__SN_; S6B-PH-SM4-TB_LF__SN__3; Mouser Part Number N/A
J11: Conn_01x02; AMASS_XT30U-F_1x02_P5.0mm_Vertical
J33, J34, J36, J37: Conn_01x02; JST_PH_S2B-PH-K_1x02_P2.00mm_Horizontal
R62: 1K; R_0603_1608Metric
S1: OS102011MA1QN1; SW_Slide_SPDT_Angled_CK_OS102011MA1Q; Manufacturer_Part_Number OS102011MA1QN1; Mouser Part Number 611-OS102011MA1QN1
TP2, TP3, TP4, TP5, TP6, TP7, TP8: TestPoint; TestPoint_Pad_D1.0mm
U7: USBLC6-2SC6; SOT-23-6

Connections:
5VDC_BUS1: J10.2, TP7.1 (1_1); also elsewhere on the board
5VDC_BUS2: J7.2, TP8.1 (1_1); also elsewhere on the board
5VDC_BUS3: J4.2, TP6.1 (1_1); also elsewhere on the board
12V_BUS1: J37.1, TP3.1 (1_1); also elsewhere on the board
12V_BUS2: J36.1, TP4.1 (1_1); also elsewhere on the board
+3V3: C13.2, J5.3, J6.4, J8.3, J9.1, S1.3, TP5.1 (1_1), U7.5 (VBUS); also elsewhere on the board
BOOT: R62.2; also elsewhere on the board
CUTTER_EN_EXT: J9.4; also elsewhere on the board
GND: C13.1, D7.2 (A), J4.1, J5.1, J6.1, J7.1, J8.1, J9.6, J10.1, J11.2, J36.2, J37.2, S1.1, U7.2 (GND); also elsewhere on the board
I2C2_SDA: J9.3; also elsewhere on the board
I2C2_SDL: J9.2; also elsewhere on the board
unnamed: R62.1, S1.2
PGM_RX: U7.1 (I/O1); also elsewhere on the board
PGM_RX_FILT: J6.2, U7.6 (I/O1)
PGM_TX: U7.3 (I/O2); also elsewhere on the board
PGM_TX_FILT: J6.3, U7.4 (I/O2)
PYR_1: J33.2; also elsewhere on the board
PYR_2: J34.2; also elsewhere on the board
VBAT+: D7.1 (K), J11.1, TP2.1 (1_1); also elsewhere on the board
VBAT_Fused_OUT: J33.1, J34.1; also elsewhere on the board
VTX_EN_EXT: J9.5; also elsewhere on the board
onewire1: J8.2; also elsewhere on the board
onewire2: J5.2; also elsewhere on the board

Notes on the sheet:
pin 2 & 3 are common
SILKSCREEN: 3V3 RX TX GND
2S CONN
BOOT MODE SWITCH
Silkscreen: ONEWIRE1
Silkscreen:ONEWIRE 2
XT-30 DIRECT SOLDER
Silkscreen:HEATER_EN
SILKSCREEN: MOD2
SILKSCREEN: MOD3
SILKSCREEN: RADIO EN
Silkscreen:VTX_EN
PROGRAMMING
FROM RADMOD

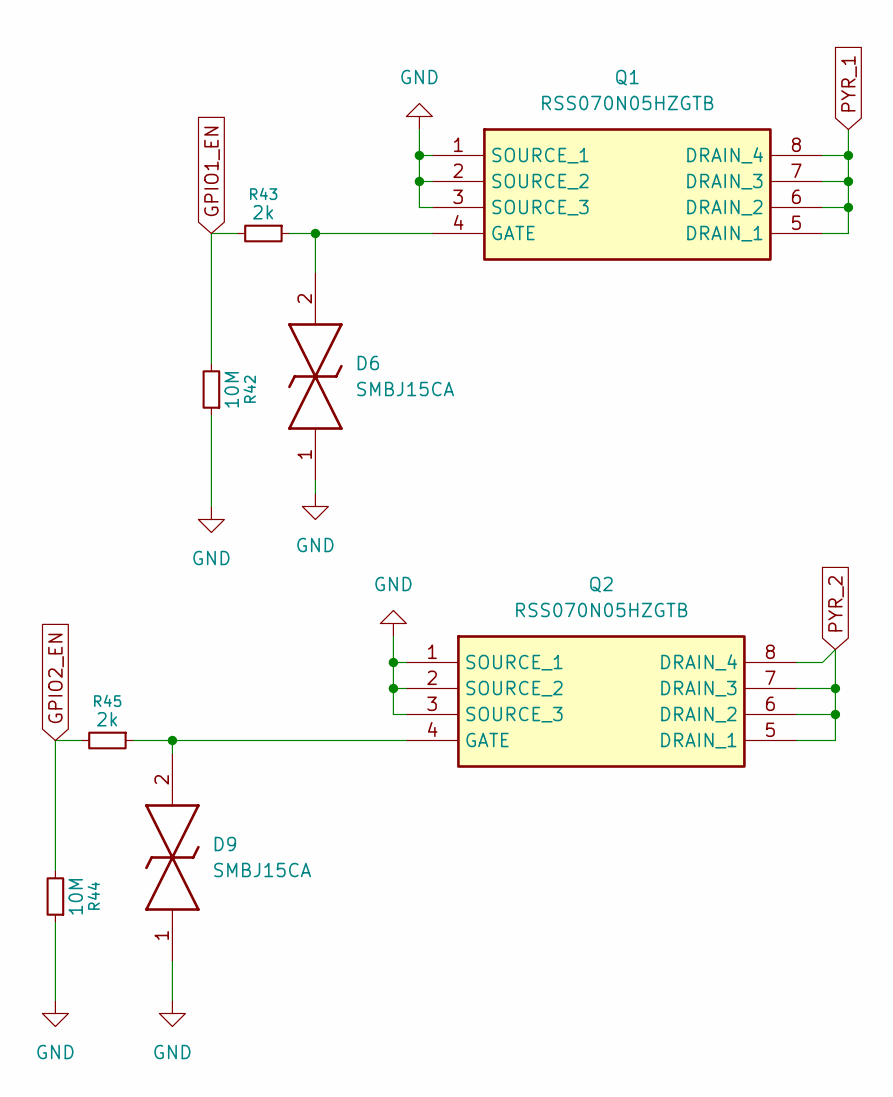
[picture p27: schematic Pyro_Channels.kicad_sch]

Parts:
D6, D9: SMBJ15CA; DIONM5436X244N; Mouser Part Number 947-SMBJ15CA
Q1, Q2: RSS070N05HZGTB; SOIC127P600X175-8N; Manufacturer_Part_Number RSS070N05HZGTB; Mouser Part Number 755-RSS070N05HZGTB
R42, R44: 10M; R_0603_1608Metric
R43, R45: 2k; R_0603_1608Metric

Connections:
GND: D6.1, D9.1, Q1.1 (SOURCE_1), Q1.2 (SOURCE_2), Q1.3 (SOURCE_3), Q2.1 (SOURCE_1), Q2.2 (SOURCE_2), Q2.3 (SOURCE_3), R42.1, R44.1; also elsewhere on the board
GPIO1_EN: R42.2, R43.2; also elsewhere on the board
GPIO2_EN: R44.2, R45.2; also elsewhere on the board
unnamed: D6.2, Q1.4 (GATE), R43.1
unnamed: D9.2, Q2.4 (GATE), R45.1
PYR_1: Q1.5 (DRAIN_1), Q1.6 (DRAIN_2), Q1.7 (DRAIN_3), Q1.8 (DRAIN_4); also elsewhere on the board
PYR_2: Q2.5 (DRAIN_1), Q2.6 (DRAIN_2), Q2.7 (DRAIN_3), Q2.8 (DRAIN_4); also elsewhere on the board

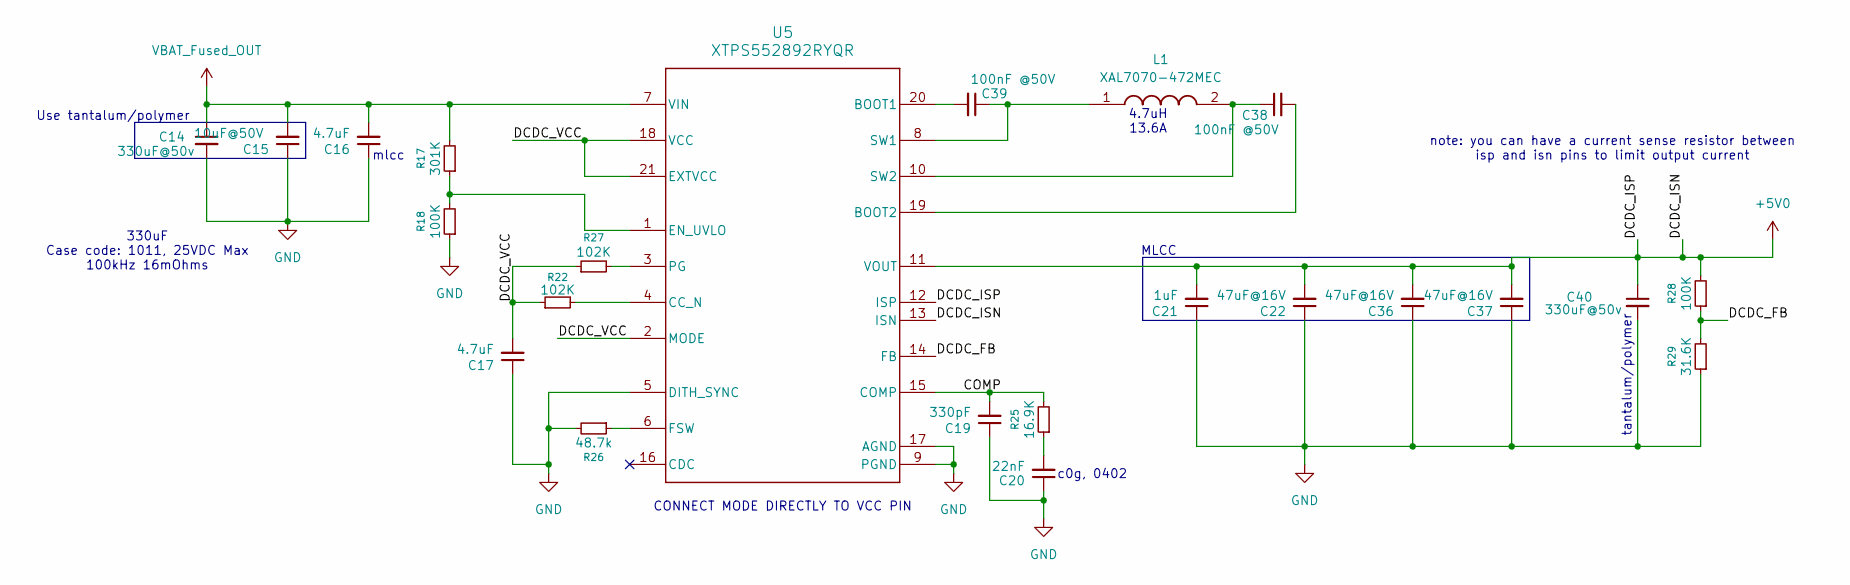
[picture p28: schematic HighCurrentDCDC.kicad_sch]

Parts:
C14, C40: 330uF@50v; CP_Radial_D10.0mm_P5.00mm; Manufacturer_Part_Number RHA1011331M025K
C15: 10uF@50V; C_1210_3225Metric; Manufacturer_Part_Number GRM32EC72A106KE05L
C16, C17: 4.7uF; C_0805_2012Metric_Pad1.18x1.45mm_HandSolder
C19: 330pF; C_0603_1608Metric
C20: 22nF; C_0603_1608Metric
C21: 1uF; C_0805_2012Metric_Pad1.18x1.45mm_HandSolder
C22, C36, C37: 47uF@16V; C_1210_3225Metric; Manufacturer_Part_Number GRM31CR61C476ME44L
C38, C39: 100nF @50V; C_0402_1005Metric_Pad0.74x0.62mm_HandSolder
L1: XAL7070-472MEC; XAL7070472MEC; Mouser Part Number 994-XAL7070-472MEC
R17: 301K; R_0603_1608Metric
R18, R28: 100K; R_0603_1608Metric
R22, R27: 102K; R_0603_1608Metric
R25: 16.9K; R_0603_1608Metric
R26: 48.7k; R_0603_1608Metric
R29: 31.6K; R_0603_1608Metric
U5: XTPS552892RYQR; RYQ0021A-MFG

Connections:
+5V0: C21.2, C22.2, C36.2, C37.2, C40.1, R28.2, U5.11 (VOUT), U5.12 (ISP), U5.13 (ISN); also elsewhere on the board
/HighCurrentDCDC/COMP: C19.2, R25.2, U5.15 (COMP)
/HighCurrentDCDC/DCDC_FB: R28.1, R29.2, U5.14 (FB)
/HighCurrentDCDC/DCDC_VCC: C17.2, R22.1, R27.1, U5.2 (MODE), U5.18 (VCC), U5.21 (EXTVCC)
GND: C14.2, C15.1, C16.1, C17.1, C19.1, C20.1, C21.1, C22.1, C36.1, C37.1, C40.2, R18.1, R26.2, R29.1, U5.5 (DITH_SYNC), U5.9 (PGND), U5.17 (AGND); also elsewhere on the board
unnamed: C20.2, R25.1
unnamed: C39.2, U5.20 (BOOT1)
unnamed: C38.2, U5.19 (BOOT2)
unnamed: R22.2, U5.4 (CC_N)
unnamed: R17.1, R18.2, U5.1 (EN_UVLO)
unnamed: R26.1, U5.6 (FSW)
unnamed: R27.2, U5.3 (PG)
unnamed: C39.1, L1.1, U5.8 (SW1)
unnamed: C38.1, L1.2, U5.10 (SW2)
VBAT_Fused_OUT: C14.1, C15.2, C16.2, R17.2, U5.7 (VIN); also elsewhere on the board

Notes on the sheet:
4.7uH 13.6A
tantalum/polymer
c0g, 0402
CONNECT MODE DIRECTLY TO VCC PIN
note: you can have a current sense resistor between isp and isn pins to limit output current
330uF Case code: 1011, 25VDC Max 100kHz 16mOhms
MLCC
Use tantalum/polymer
mlcc

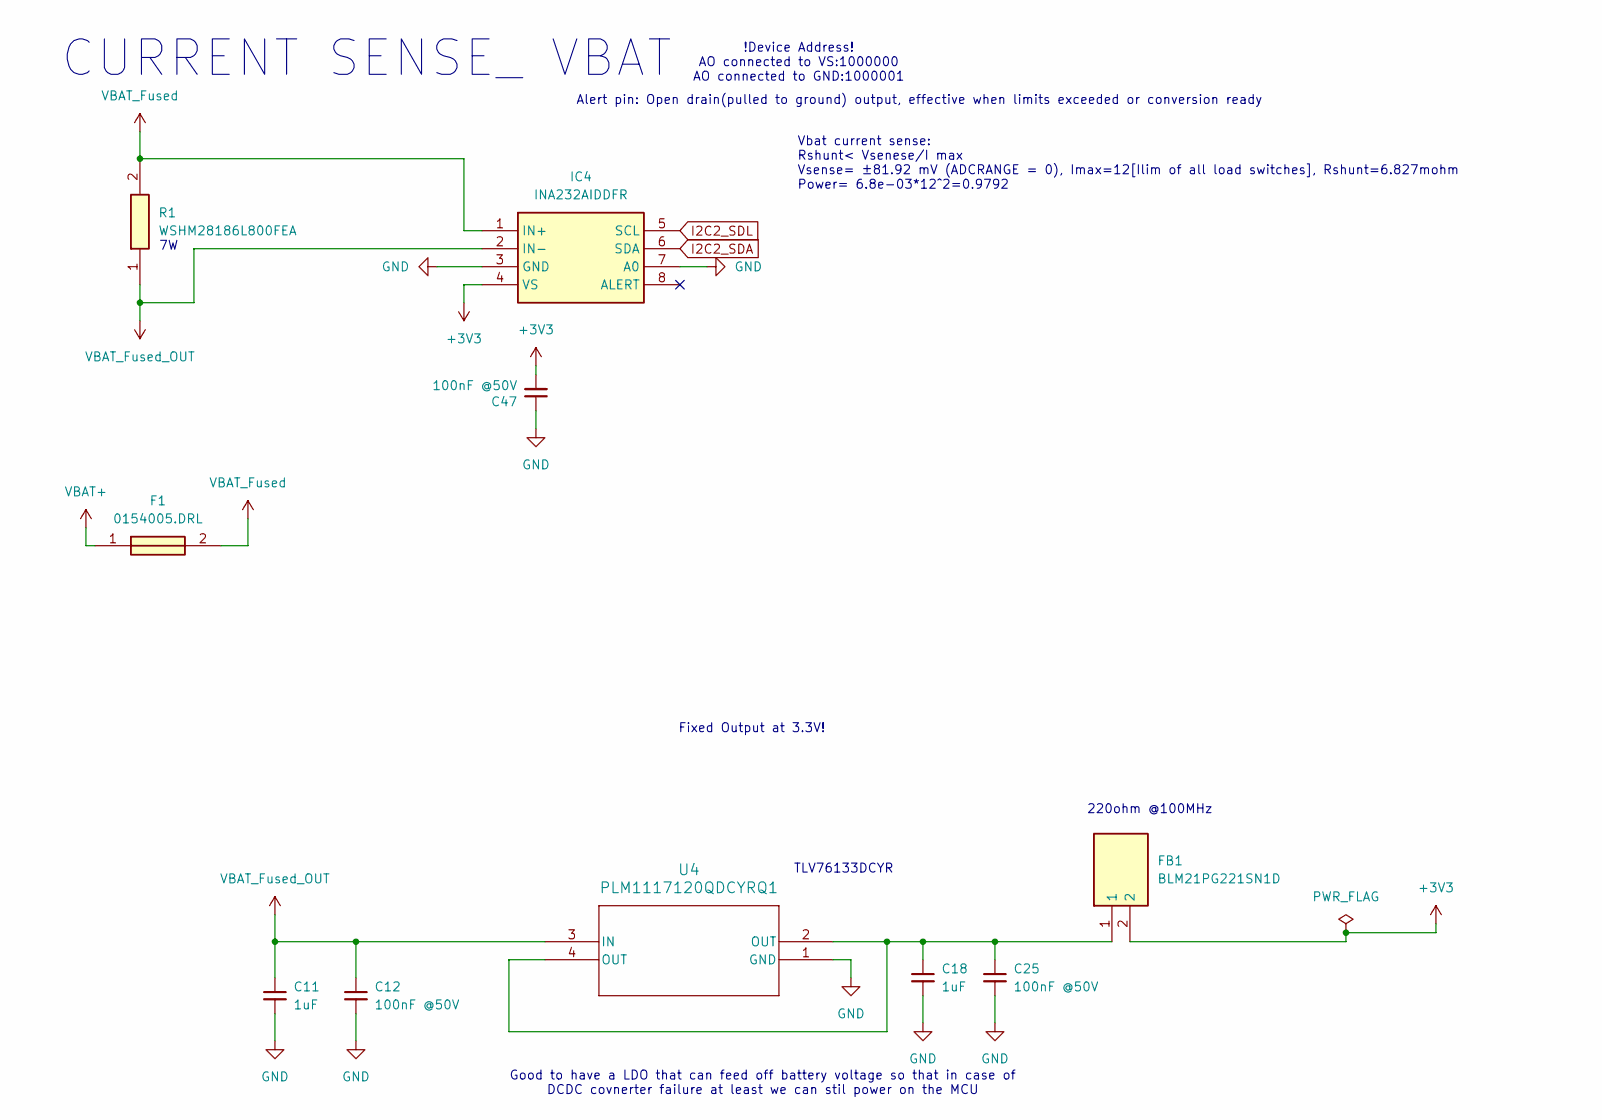
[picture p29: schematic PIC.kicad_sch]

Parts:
C11, C18: 1uF; C_0603_1608Metric
C12, C25: 100nF @50V; C_0603_1608Metric
C47: 100nF @50V; C_0402_1005Metric_Pad0.74x0.62mm_HandSolder
F1: 0154005.DRL; 0154005DRL; Manufacturer_Part_Number 0154005.DRL; Mouser Part Number 576-0154005.DRL
FB1: BLM21PG221SN1D; BEADC2012X105N; Manufacturer_Part_Number BLM21PG221SN1D; Mouser Part Number 81-BLM21P221SG
IC4: INA232AIDDFR; SOT65P280X110-8N; Manufacturer_Part_Number INA232AIDDFR; Mouser Part Number 595-INA232AIDDFR
R1: WSHM28186L800FEA; WSHM2818R0330FEB; Manufacturer_Part_Number WSHM28186L800FEA; Mouser Part Number 71-WSHM28186L800FEA
U4: PLM1117120QDCYRQ1; SOT-223-4_DCY_TEX

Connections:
+3V3: C47.2, FB1.2, IC4.4 (VS); also elsewhere on the board
GND: C11.2, C12.2, C18.2, C25.2, C47.1, IC4.3 (GND), IC4.7 (A0), U4.1 (GND); also elsewhere on the board
I2C2_SDA: IC4.6 (SDA); also elsewhere on the board
I2C2_SDL: IC4.5 (SCL); also elsewhere on the board
unnamed: C18.1, C25.1, FB1.1, U4.2 (OUT), U4.4 (OUT)
VBAT+: F1.1; also elsewhere on the board
VBAT_Fused: F1.2, IC4.1 (IN+), R1.2
VBAT_Fused_OUT: C11.1, C12.1, IC4.2 (IN-), R1.1, U4.3 (IN); also elsewhere on the board

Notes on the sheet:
CURRENT SENSE_ VBAT
TLV76133DCYR
!Device Address! AO connected to VS:1000000 AO connected to GND:1000001
Vbat current sense: Rshunt< Vsenese/I max Vsense= ±81.92 mV (ADCRANGE = 0), Imax=12[Ilim of all load switches], Rshunt=6.827mohm Power= 6.8e-03*12^2=0.9792
220ohm @100MHz
Alert pin: Open drain(pulled to ground) output, effective when limits exceeded or conversion ready
Fixed Output at 3.3V!
Good to have a LDO that can feed off battery voltage so that in case of DCDC covnerter failure at least we can stil power on the MCU

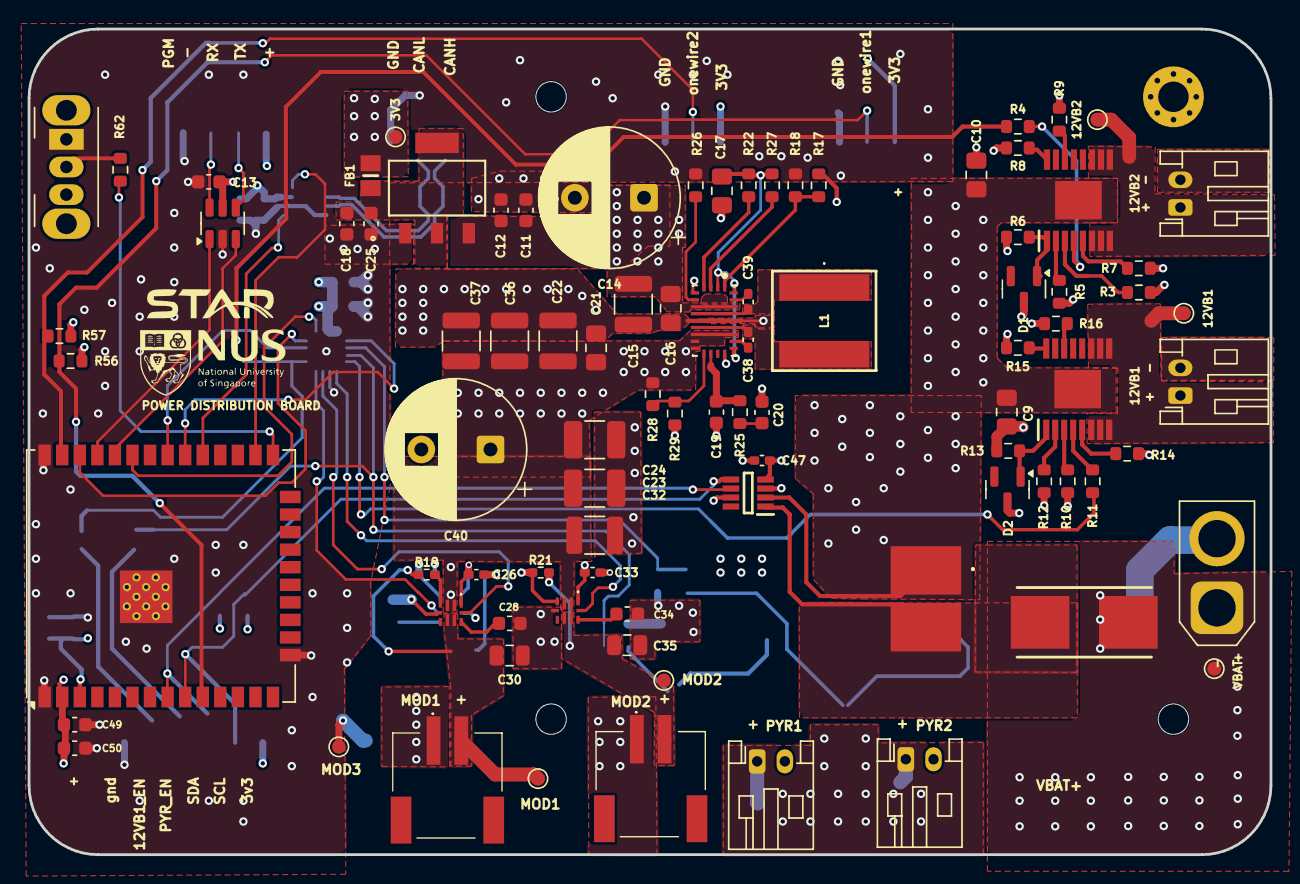
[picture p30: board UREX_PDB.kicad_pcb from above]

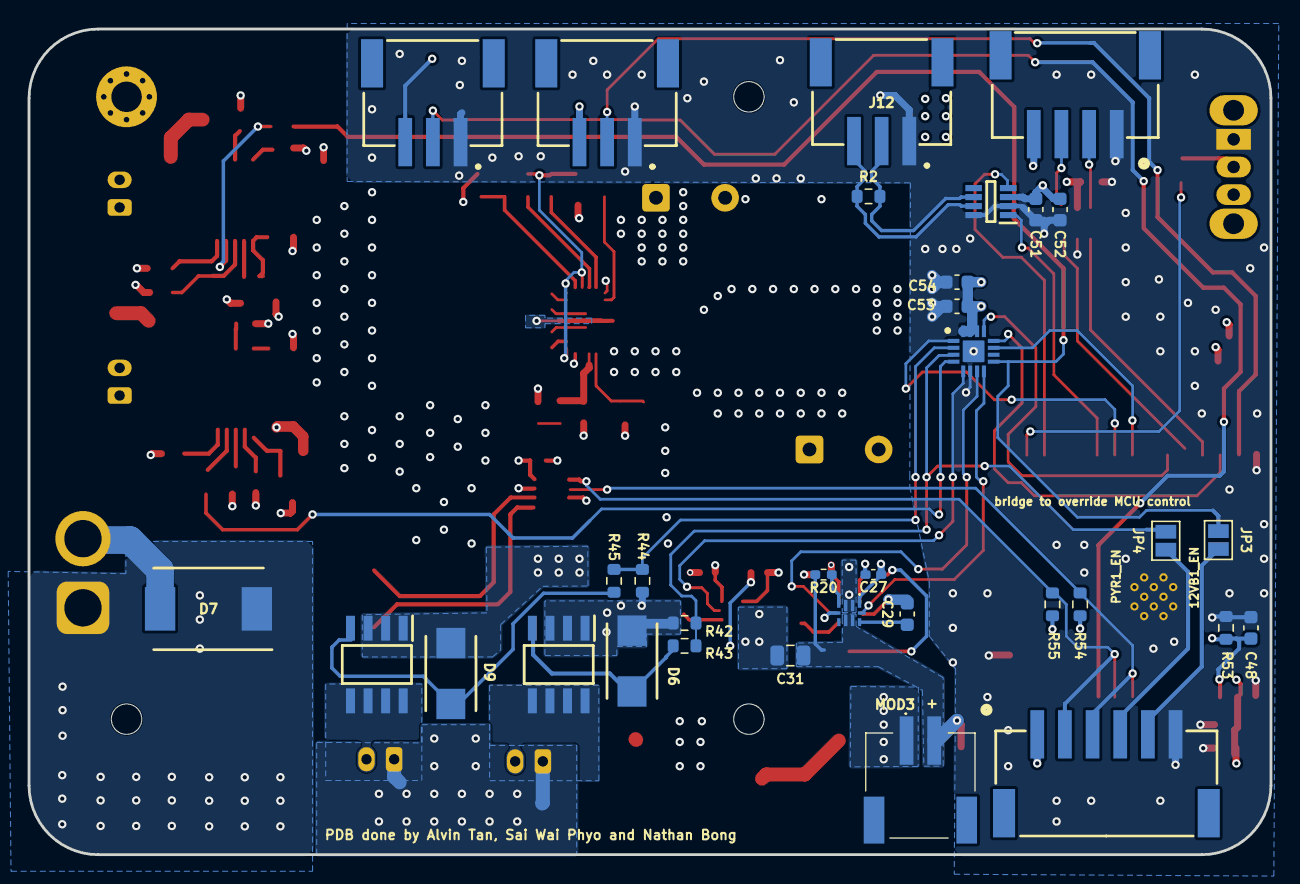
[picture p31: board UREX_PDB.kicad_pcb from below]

Board: 4 copper layers, 89.8 x 59.7 mm, 126 parts (33 on the bottom side), 75 nets.

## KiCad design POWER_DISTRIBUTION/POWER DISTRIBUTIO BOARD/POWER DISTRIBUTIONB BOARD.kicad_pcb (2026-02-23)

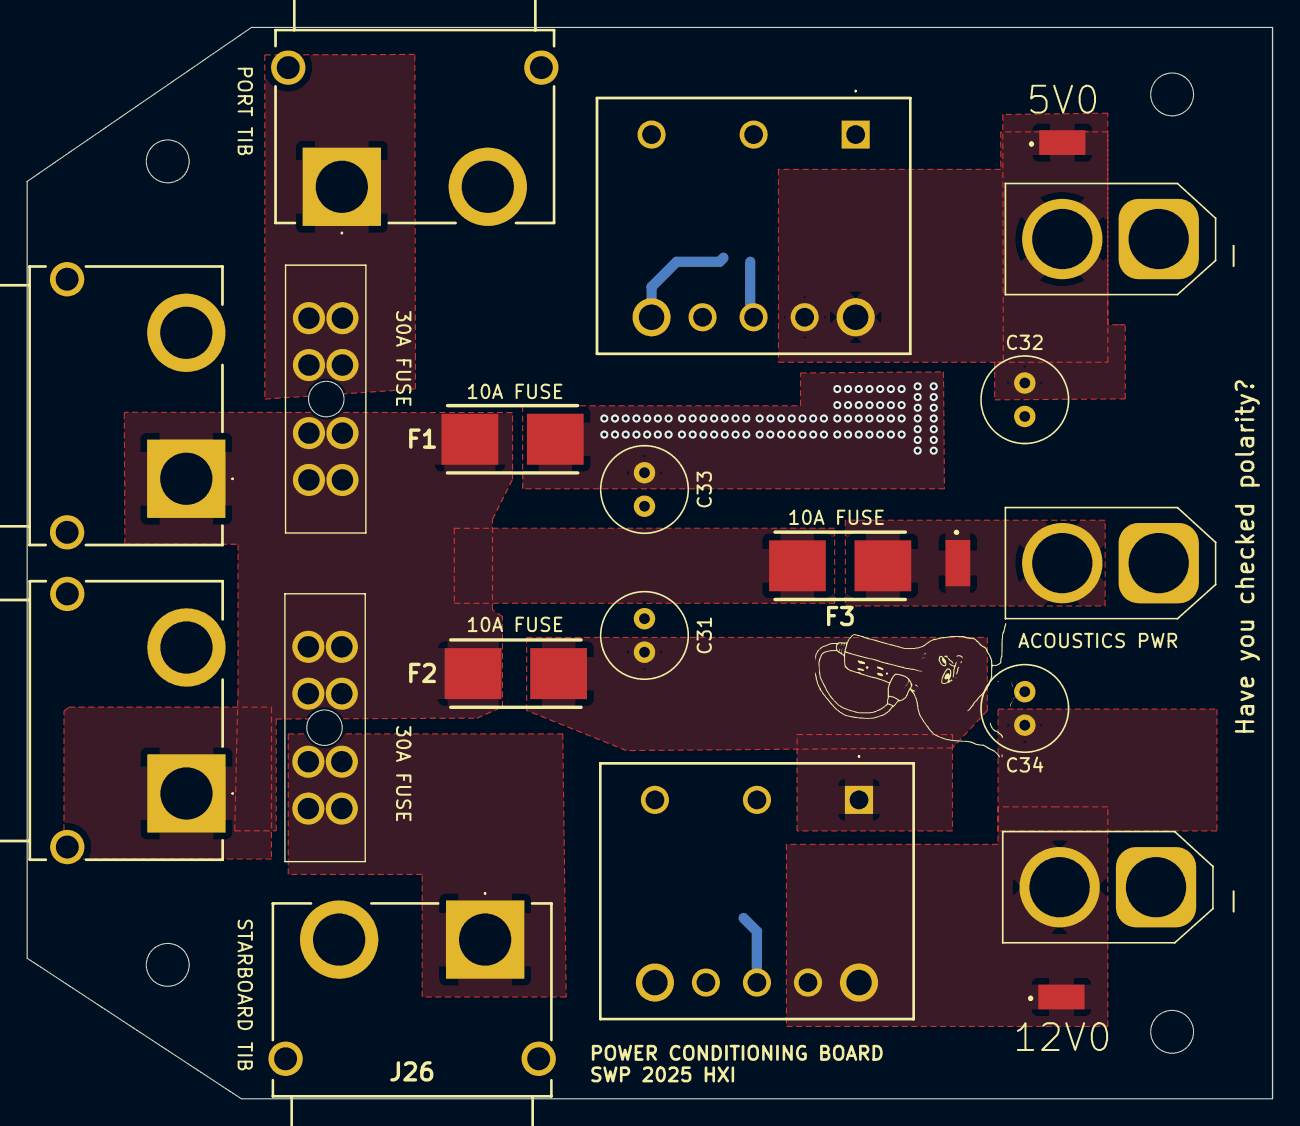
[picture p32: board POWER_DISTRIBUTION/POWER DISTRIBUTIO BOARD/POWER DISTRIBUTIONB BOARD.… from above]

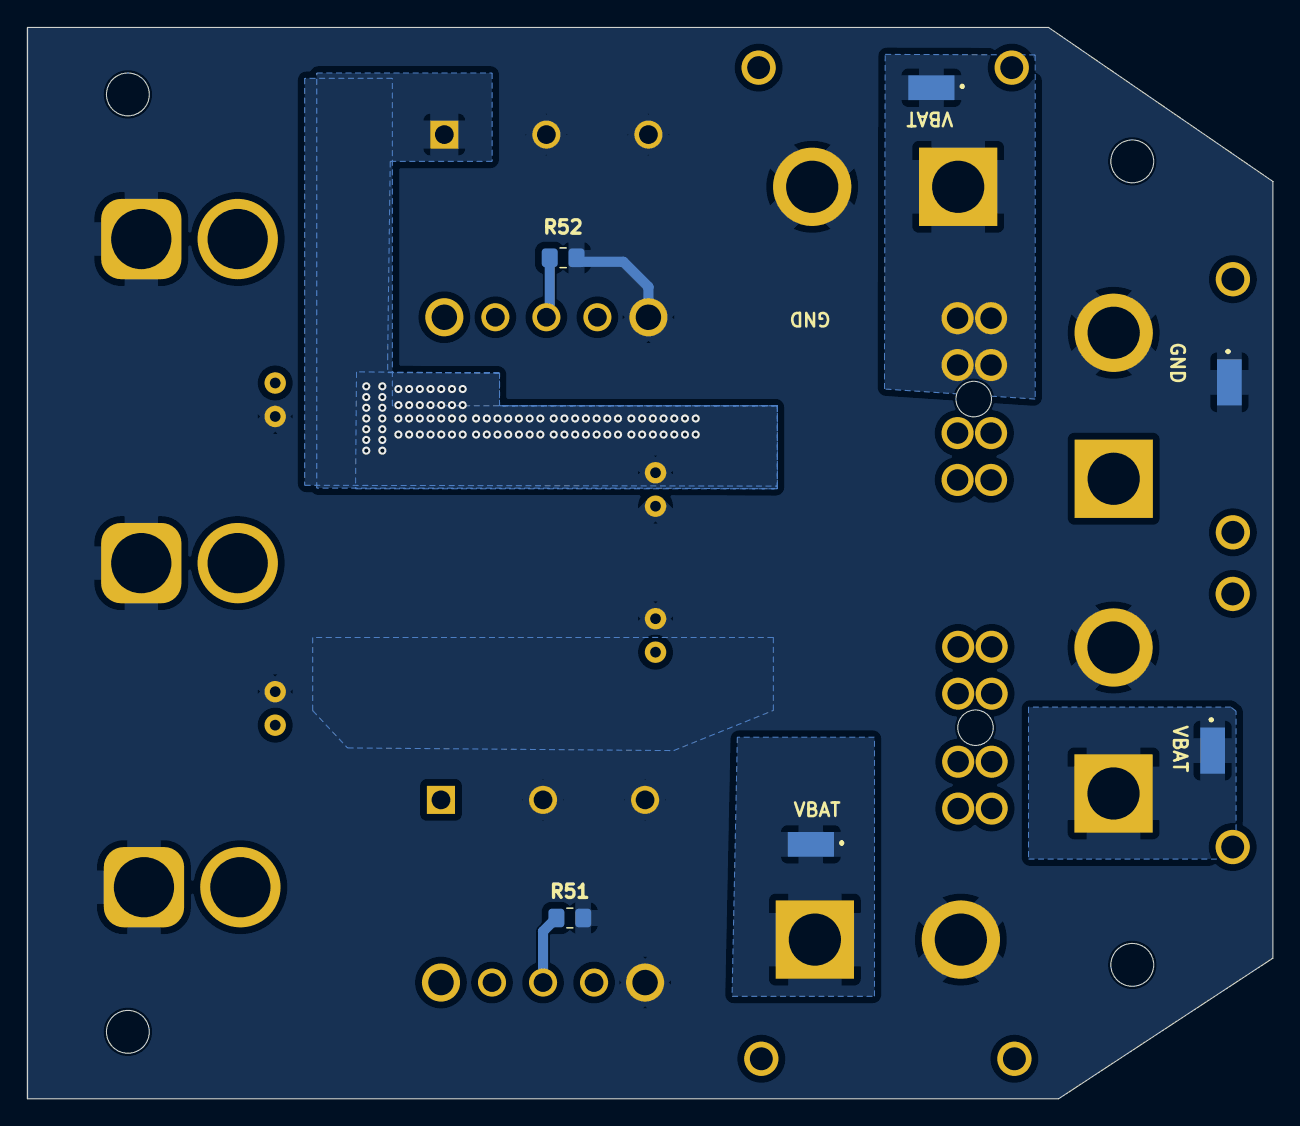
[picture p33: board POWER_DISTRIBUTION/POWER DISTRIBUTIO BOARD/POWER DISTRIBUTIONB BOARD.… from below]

Board: 2 copper layers, 93.0 x 80.0 mm, 31 parts (6 on the bottom side), 9 nets.

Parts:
C31, C32, C33, C34: 47u; C_Radial_D6.3mm_H5.0mm_P2.50mm
F1, F2, F3: 0154010.DR; 0154001.DRT
H1, H2, H3, H4: MountingHole; MountingHole_3.2mm_M3_ISO7380
J1, J4, J7: Conn_01x02_Socket; AMASS_XT60-F_1x02_P7.20mm_Vertical
J25, J26, J27, J28: XT90PW-F; XT90PWF
PS3, PS4: RPMA5.0-8.0_OF; RPMA5080OF
R51: 1k82; R_0805_2012Metric_Pad1.20x1.40mm_HandSolder
R52: 8k66; R_0805_2012Metric_Pad1.20x1.40mm_HandSolder
TP3, TP4, TP5, TP6, TP7, TP8, TP24: S1751-46R; S175146R
U2, U3: 178.6165.0002; 17861650002

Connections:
+5V: C32.1, J7.2, PS4.7 (+SENSE), PS4.8 (+VOUT), TP5.1
+12V: C34.1, J1.2, PS3.7 (+SENSE), PS3.8 (+VOUT), TP3.1
GND: C31.2, C32.2, C33.2, C34.2, J1.1, J4.1, J7.1, J25.2 (-), J26.2 (-), J27.2 (-), J28.2 (-), PS3.2 (CTRL), PS3.3 (-VIN), PS3.4 (-VOUT), PS4.2 (CTRL), PS4.3 (-VIN), PS4.4 (-VOUT), R51.2, R52.2, TP7.1
unnamed: PS3.6 (TRIM), R51.1
unnamed: PS4.6 (TRIM), R52.1
VBAT+: C31.1, C33.1, F1.1, F1.2, F2.1, F2.2, F3.1, J27.1 (+), J28.1 (+), PS3.1 (+VIN), PS4.1 (+VIN), TP6.1, U2.5, U2.6, U2.7, U2.8, U3.5, U3.6, U3.7, U3.8
VBAT_A_FUSED: F3.2, J4.2, TP4.1
VBAT_FUSED: J26.1 (+), TP8.1, U3.1, U3.2, U3.3, U3.4
VBAT_P_FUSED: J25.1 (+), TP24.1, U2.1, U2.2, U2.3, U2.4

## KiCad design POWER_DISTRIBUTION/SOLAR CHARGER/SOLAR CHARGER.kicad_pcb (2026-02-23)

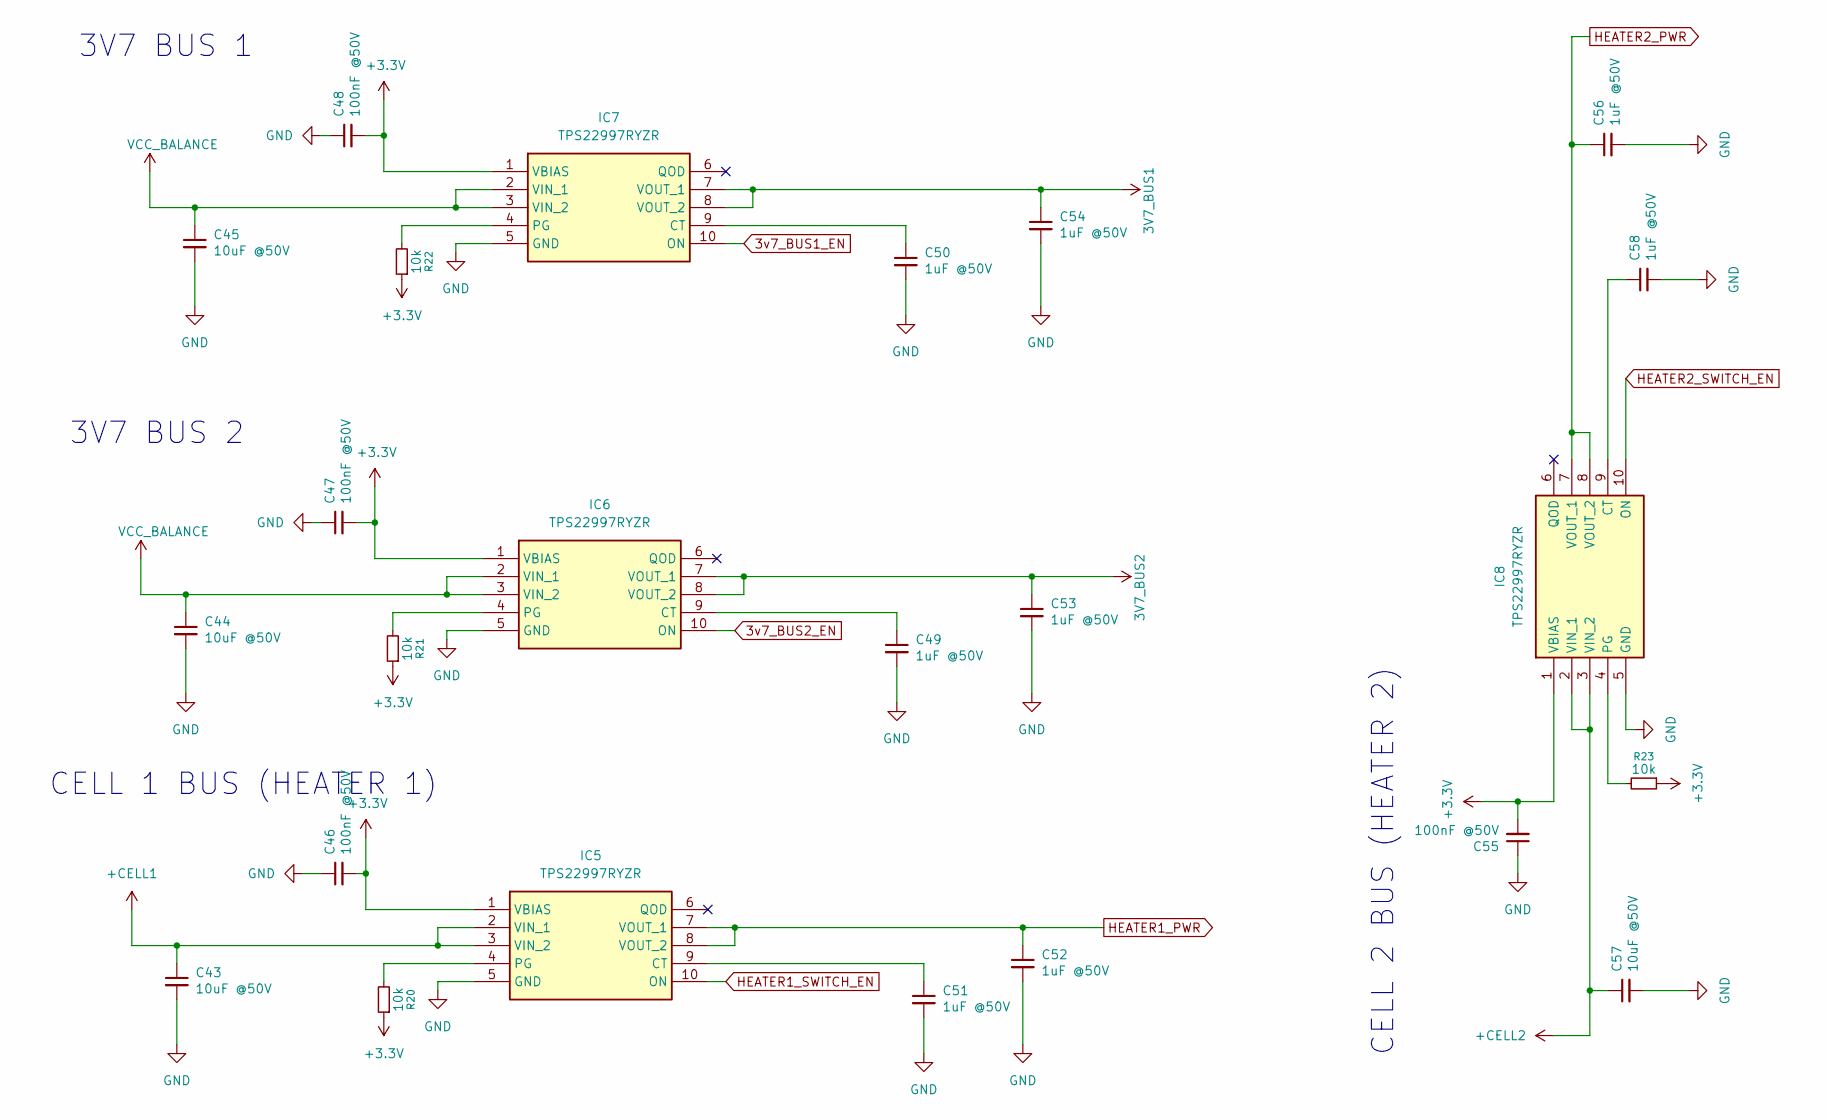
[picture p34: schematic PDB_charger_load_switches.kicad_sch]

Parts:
C43, C44, C45, C57: 10uF @50V; C_1210_3225Metric_Pad1.33x2.70mm_HandSolder
C46, C47, C48, C55: 100nF @50V; C_0402_1005Metric_Pad0.74x0.62mm_HandSolder
C49, C50, C51, C52, C53, C54, C56, C58: 1uF @50V; C_0805_2012Metric_Pad1.18x1.45mm_HandSolder
IC5, IC6, IC7, IC8: TPS22997RYZR; Mouser Part Number 595-TPS22997RYZR
R20, R21, R22, R23: 10k; R_0402_1005Metric_Pad0.72x0.64mm_HandSolder

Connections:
3V7_BUS1: C54.1, IC7.7 (VOUT_1), IC7.8 (VOUT_2); also elsewhere on the board
3V7_BUS2: C53.1, IC6.7 (VOUT_1), IC6.8 (VOUT_2); also elsewhere on the board
3v7_BUS1_EN: IC7.10 (ON); also elsewhere on the board
3v7_BUS2_EN: IC6.10 (ON); also elsewhere on the board
+3.3V: C46.2, C47.2, C48.2, C55.2, IC5.1 (VBIAS), IC6.1 (VBIAS), IC7.1 (VBIAS), IC8.1 (VBIAS), R20.1, R21.1, R22.1, R23.1; also elsewhere on the board
+CELL1: C43.1, IC5.2 (VIN_1), IC5.3 (VIN_2); also elsewhere on the board
+CELL2: C57.1, IC8.2 (VIN_1), IC8.3 (VIN_2); also elsewhere on the board
GND: C43.2, C44.2, C45.2, C46.1, C47.1, C48.1, C49.2, C50.2, C51.2, C52.2, C53.2, C54.2, C55.1, C56.2, C57.2, C58.2, IC5.5 (GND), IC6.5 (GND), IC7.5 (GND), IC8.5 (GND); also elsewhere on the board
HEATER1_PWR: C52.1, IC5.7 (VOUT_1), IC5.8 (VOUT_2); also elsewhere on the board
HEATER1_SWITCH_EN: IC5.10 (ON); also elsewhere on the board
HEATER2_PWR: C56.1, IC8.7 (VOUT_1), IC8.8 (VOUT_2); also elsewhere on the board
HEATER2_SWITCH_EN: IC8.10 (ON); also elsewhere on the board
unnamed: C51.1, IC5.9 (CT)
unnamed: IC5.4 (PG), R20.2
unnamed: C49.1, IC6.9 (CT)
unnamed: IC6.4 (PG), R21.2
unnamed: C50.1, IC7.9 (CT)
unnamed: IC7.4 (PG), R22.2
unnamed: C58.1, IC8.9 (CT)
unnamed: IC8.4 (PG), R23.2
VCC_BALANCE: C44.1, C45.1, IC6.2 (VIN_1), IC6.3 (VIN_2), IC7.2 (VIN_1), IC7.3 (VIN_2); also elsewhere on the board

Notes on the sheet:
3V7 BUS 2
CELL 2 BUS (HEATER 2)
CELL 1 BUS (HEATER 1)
3V7 BUS 1

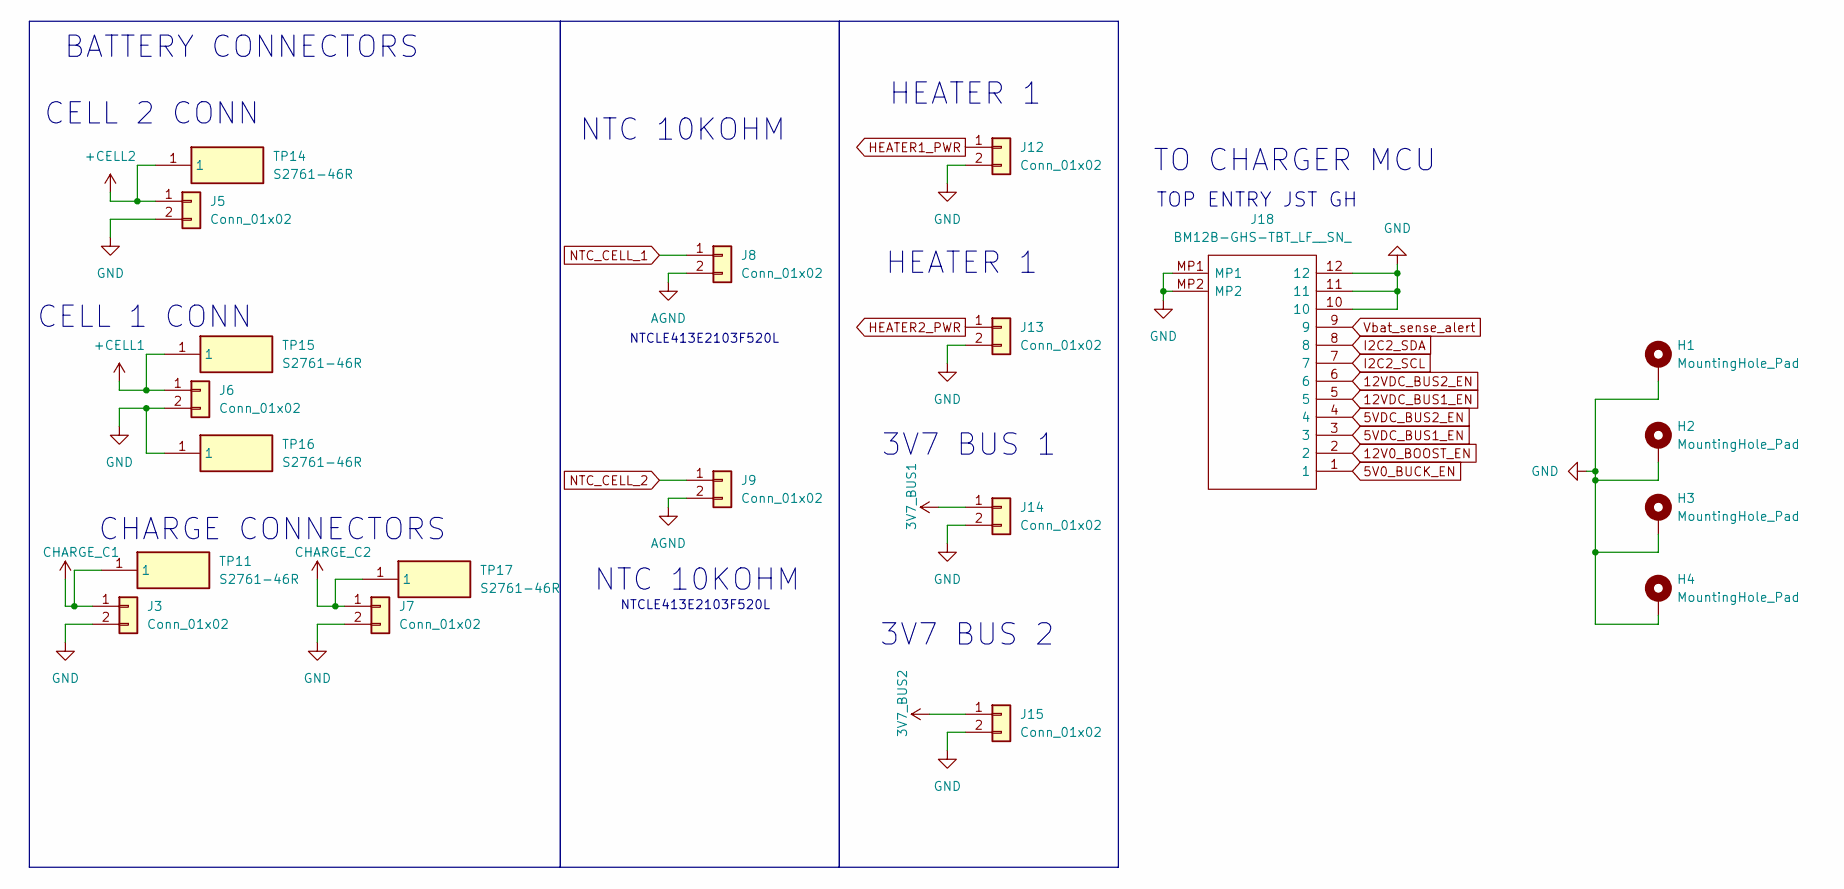
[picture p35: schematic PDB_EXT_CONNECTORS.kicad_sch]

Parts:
H1, H2, H3, H4: MountingHole_Pad; MountingHole_3.2mm_M3_Pad_Via
J3, J5, J6, J7: Conn_01x02; JST_PH_S2B-PH-K_1x02_P2.00mm_Horizontal
J8, J9: Conn_01x02; SolderWire-0.127sqmm_1x02_P3.7mm_D0.48mm_OD1mm
J12, J13, J14, J15: Conn_01x02; JST_PH_B2B-PH-K_1x02_P2.00mm_Vertical
J18: BM12B-GHS-TBT_LF__SN_; BM12BGHSTBTLFSN; Mouser Part Number 306-BM12BGHSTBTLFSNN
TP11, TP14, TP15, TP16, TP17: S2761-46R; S276146R; Mouser Part Number 855-S2761-46R

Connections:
3V7_BUS1: J14.1; also elsewhere on the board
3V7_BUS2: J15.1; also elsewhere on the board
5V0_BUCK_EN: J18.1; also elsewhere on the board
5VDC_BUS1_EN: J18.3; also elsewhere on the board
5VDC_BUS2_EN: J18.4; also elsewhere on the board
12V0_BOOST_EN: J18.2; also elsewhere on the board
12VDC_BUS1_EN: J18.5; also elsewhere on the board
12VDC_BUS2_EN: J18.6; also elsewhere on the board
+CELL1: J6.1, TP15.1; also elsewhere on the board
+CELL2: J5.1, TP14.1; also elsewhere on the board
AGND: J8.2, J9.2
CHARGE_C1: J3.1, TP11.1; also elsewhere on the board
CHARGE_C2: J7.1, TP17.1; also elsewhere on the board
GND: H1.1, H2.1, H3.1, H4.1, J3.2, J5.2, J6.2, J7.2, J12.2, J13.2, J14.2, J15.2, J18.10, J18.11, J18.12, J18.MP1, J18.MP2, TP16.1; also elsewhere on the board
HEATER1_PWR: J12.1; also elsewhere on the board
HEATER2_PWR: J13.1; also elsewhere on the board
I2C2_SCL: J18.7; also elsewhere on the board
I2C2_SDA: J18.8; also elsewhere on the board
NTC_CELL_1: J8.1; also elsewhere on the board
NTC_CELL_2: J9.1; also elsewhere on the board
Vbat_sense_alert: J18.9; also elsewhere on the board

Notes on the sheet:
TO CHARGER MCU
HEATER 1
TOP ENTRY JST GH
CELL 2 CONN
3V7 BUS 1
NTC 10KOHM
NTCLE413E2103F520L
CELL 1 CONN
BATTERY CONNECTORS
3V7 BUS 2
CHARGE CONNECTORS


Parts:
C36: 100nF @50V; C_0402_1005Metric_Pad0.74x0.62mm_HandSolder
C37, C38: 1uF @50V; C_0805_2012Metric_Pad1.18x1.45mm_HandSolder
D7: PESD2CANFD24V-UX; SOT65P210X110-3N; Mouser Part Number 771-PESD2CANFD24V-UX
IC4: SN65HVD233QDRQ1; SOIC127P600X175-8N; Mouser Part Number 595-SN65HVD233QDRQ1
J10: Conn_01x02; JST_PH_B2B-PH-K_1x02_P2.00mm_Vertical
J11: Conn_01x03; PinHeader_1x03_P2.54mm_Vertical
R18, R19: 60; R_0603_1608Metric

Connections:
+3.3V: C36.2, C37.2, IC4.3 (VCC), J11.1; also elsewhere on the board
CAN+: D7.2 (K2), IC4.7 (CANH), J10.1, R18.2
CAN-: D7.1 (K1), IC4.6 (CANL), J10.2, R19.1
CAN_RX: IC4.1 (TXD); also elsewhere on the board
CAN_TX: IC4.4 (RXD); also elsewhere on the board
GND: C36.1, C37.1, C38.1, D7.3 (CC), IC4.2 (GND), J11.3; also elsewhere on the board
unnamed: C38.2, R18.1, R19.2
RS: IC4.8 (RS), J11.2

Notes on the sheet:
Connect RS to VCC for high speed, GND for low power
CURRENT SENSE_ VBAT


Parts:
C19, C20: 10uF @50V; C_1210_3225Metric_Pad1.33x2.70mm_HandSolder
C21, C22: 47uF @16VDC; C_1206_3216Metric_Pad1.33x1.80mm_HandSolder
D5, D6: PTVS3V3D1BALYL; PESD5V0S1BL315; Mouser Part Number 771-PTVS3V3D1BALYL
IC1, IC2: LTC4451AV#TRMPBF; LTC4451AVTRMPBF; Mouser Part Number 584-LTC4451AVTRMPBF
TP9, TP10: S2761-46R; S276146R; Mouser Part Number 855-S2761-46R

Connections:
GND: C19.2, C20.2, C21.2, C22.2, D5.1 (K1), D6.1 (K1), IC1.1 (VCC), IC1.14 (GND), IC2.1 (VCC), IC2.14 (GND); also elsewhere on the board
SYS_C1: C19.1, D5.2 (K2), IC1.2 (IN_1), IC1.3 (IN_2), IC1.4 (IN_3), IC1.5 (IN_4), IC1.6 (IN_5), IC1.7 (IN_6), IC1.16 (SHDN#), IC1.17 (IN_7); also elsewhere on the board
SYS_C2: C20.1, D6.2 (K2), IC2.2 (IN_1), IC2.3 (IN_2), IC2.4 (IN_3), IC2.5 (IN_4), IC2.6 (IN_5), IC2.7 (IN_6), IC2.16 (SHDN#), IC2.17 (IN_7); also elsewhere on the board
VCC_BALANCE: C21.1, C22.1, IC1.8 (OUT_1), IC1.9 (OUT_2), IC1.10 (OUT_3), IC1.11 (OUT_4), IC1.12 (OUT_5), IC1.13 (OUT_6), IC1.18 (OUT_7), IC2.8 (OUT_1), IC2.9 (OUT_2), IC2.10 (OUT_3), IC2.11 (OUT_4), IC2.12 (OUT_5), IC2.13 (OUT_6), IC2.18 (OUT_7), TP9.1, TP10.1; also elsewhere on the board

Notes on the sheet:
BATTERY BALANCE OUTPUT
3*3e-6/(5%*4.2)-0.003@1.2MHz*3= 44uF
Switches supply to cell with highest voltage when difference in voltage between Cells(V_sys pin output) is >20mV
3V7 bus draws 2.5A max when ESP32 has wifi turned on Iload=3A max
CLOAD ≥ (ILOAD(MAX) • 3μs)/ (ΔVOUT(DROOP) -ESR •ILOAD(MAX))


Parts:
C1, C2, C3, C4, C6, C7, C8, C10, C13, C14: 47uF @16VDC; C_1206_3216Metric_Pad1.33x1.80mm_HandSolder
C5, C9, C15, C16, C17, C18: 10uF @50V; C_1210_3225Metric_Pad1.33x2.70mm_HandSolder
C11, C12: 1uF @50V; C_0805_2012Metric_Pad1.18x1.45mm_HandSolder
D1, D2: PTVS3V3D1BALYL; PESD5V0S1BL315; Mouser Part Number 771-PTVS3V3D1BALYL
D3, D4: LED; LED_0603_1608Metric_Pad1.05x0.95mm_HandSolder
F1, F2: 0154005.DR; 0154005DR; Mouser Part Number 576-0154005.DR
L1, L2: SRR6838A-1R0Y; INDPM6868X420N; Manufacturer_Part_Number SRR6838A-1R0Y
R1, R2, R3, R4, R9, R10: 10k; R_0402_1005Metric_Pad0.72x0.64mm_HandSolder
R5, R6: 20K; R_0603_1608Metric
R7, R8: 100K; R_0603_1608Metric
TP1, TP2, TP7, TP8: TestPoint_Alt; TestPoint_THTPad_1.0x1.0mm_Drill0.5mm
TP3, TP4, TP5, TP6: TestPoint_Alt; TestPoint_THTPad_1.0x1.0mm_Drill0.5mm; not fitted
U1, U2: MP2731GQC-0000-P; QFN-26_MP2731

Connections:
+CELL1: F1.2; also elsewhere on the board
+CELL2: F2.2; also elsewhere on the board
CELL1_INT: TP4.1, U1.10 (INT); also elsewhere on the board
CELL1_STAT: D3.1 (K), TP6.1, U1.9 (STAT); also elsewhere on the board
CELL2_INT: TP3.1, U2.10 (INT); also elsewhere on the board
CELL2_STAT: D4.1 (K), TP5.1, U2.9 (STAT); also elsewhere on the board
CHARGE_C1: C11.2, U1.2 (IN); also elsewhere on the board
CHARGE_C2: C12.2, U2.2 (IN); also elsewhere on the board
GND: C1.2, C2.2, C3.2, C4.2, C5.1, C9.1, C11.1, C12.1, C13.2, C14.2, C15.2, C16.2, C17.2, C18.2, D1.2 (K2), D2.2 (K2), R5.1, R6.1, U1.5 (PGND), U1.6 (PGND), U1.7 (PGND), U1.15 (AGND), U1.18 (*CE), U1.23 (OTG), U2.5 (PGND), U2.6 (PGND), U2.7 (PGND), U2.15 (AGND), U2.18 (*CE), U2.23 (OTG); also elsewhere on the board
I2C1_SCL: U1.19 (SCL), U1.20 (SCL), U2.19 (SCL), U2.20 (SCL); also elsewhere on the board
I2C1_SDA: U1.21 (SDA), U2.21 (SDA); also elsewhere on the board
NTC_CELL_1: R1.2; also elsewhere on the board
NTC_CELL_2: R3.1; also elsewhere on the board
unnamed: C13.1, D1.1 (K1), F1.1, U1.17 (BATT)
unnamed: C14.1, D2.1 (K1), F2.1, U2.17 (BATT)
unnamed: D3.2 (A), R9.2
unnamed: D4.2 (A), R10.2
unnamed: C7.1, C10.2, U1.8 (BST)
unnamed: R7.1, U1.22 (DISC)
unnamed: R5.2, U1.24 (ILIM)
unnamed: R1.1, R2.2, U1.11 (NTC)
unnamed: C5.2, U1.3 (PMID)
unnamed: C7.2, C10.1, L2.2, U1.4 (SW)
unnamed: R2.1, U1.12 (VNTC)
unnamed: C6.1, C8.2, U2.8 (BST)
unnamed: R8.1, U2.22 (DISC)
unnamed: R6.2, U2.24 (ILIM)
unnamed: R3.2, R4.1, U2.11 (NTC)
unnamed: C9.2, U2.3 (PMID)
unnamed: C6.2, C8.1, L1.2, U2.4 (SW)
unnamed: R4.2, U2.12 (VNTC)
SYS_C1: C1.1, C3.1, L2.1, TP2.1, U1.16 (SYS); also elsewhere on the board
SYS_C2: C2.1, C4.1, L1.1, TP1.1, U2.16 (SYS); also elsewhere on the board
VREF_1: C15.1, C17.1, R7.2, R9.1, TP7.1, U1.13 (VREF), U1.14 (VREF)
VREF_2: C16.1, C18.1, R8.2, R10.1, TP8.1, U2.13 (VREF), U2.14 (VREF)

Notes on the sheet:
reverse polarity+ESD breakdown voltage=4.5V
47uF caps are actually 22uF at 3V7!
I LIMIT= 120/20(KOHM) =6 [A]
CELL 1
1-2 BRIDGET TO EN LED 2-3 TO DISABLE LED(SAVE POWER)
CELL 2
Vref=3.6V, max current= 40mA, DO NOT USE FOR MCU Minimum system regulation voltage (I2C)=3.82V Switching Freq= 1.1-1.6MHz Batfet Rds=14mohm Input minimum voltage regulation (I2C) = 3.7V Thermal Shutdown hysterisis=20degreeC Decoupling Capacitor requirement= 47uF
system voltage output
1.0uH @5.7A
reverse polarity+ESD breakdown voltage=4.5V
STATUS LED EN/DISABLE
CE is set low, charging always enabled


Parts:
C23, C24: 20p; C_0402_1005Metric_Pad0.74x0.62mm_HandSolder
C25, C26, C27, C28, C29, C30, C31, C34, C39, C42: 100nF @50V; C_0402_1005Metric_Pad0.74x0.62mm_HandSolder
C33, C40, C41: 1uF @50V; C_0805_2012Metric_Pad1.18x1.45mm_HandSolder
FB1: BLM18AG601SN1D; BLM18SP221SN1B; Mouser Part Number 81-BLM11A601S
FB2: BLM21PG221SN1D; BEADC2012X105N; Mouser Part Number 81-BLM21P221SG
J1: Conn_01x03_Socket; PinHeader_1x03_P2.54mm_Vertical
J2: Conn_ARM_JTAG_SWD_10; PinHeader_2x05_P1.27mm_Horizontal
PS1: TLV75733PDBVR; SOT95P280X145-5N; Mouser Part Number 595-TLV75733PDBVR
R11: 1M; R_0603_1608Metric
R12: 10k; R_0402_1005Metric_Pad0.72x0.64mm_HandSolder
R13, R14, R15, R16: 2.4k; R_0603_1608Metric
S1: OS102011MA1QN1; Mouser Part Number 611-OS102011MA1QN1
TP12: TestPoint_Alt; TestPoint_THTPad_1.0x1.0mm_Drill0.5mm
U3: STM32F103RGTx; LQFP-64_10x10mm_P0.5mm
Y1: Crystal; Crystal_SMD_5032-2Pin_5.0x3.2mm

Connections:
3v7_BUS1_EN: U3.22 (PA6); also elsewhere on the board
3v7_BUS2_EN: U3.23 (PA7); also elsewhere on the board
5V0_BUCK_EN: U3.35 (PB14); also elsewhere on the board
5VDC_BUS1_EN: U3.39 (PC8); also elsewhere on the board
5VDC_BUS2_EN: U3.38 (PC7); also elsewhere on the board
12V0_BOOST_EN: U3.36 (PB15); also elsewhere on the board
12VDC_BUS1_EN: U3.20 (PA4); also elsewhere on the board
12VDC_BUS2_EN: U3.21 (PA5); also elsewhere on the board
+3.3V: C25.2, C26.2, C28.2, C29.2, C30.2, C31.2, C33.2, C34.1, FB1.1, FB2.2, J1.1, J2.1 (VTref), R13.2, R14.2, R15.2, R16.2, TP12.1, U3.1 (VBAT), U3.13 (VDDA), U3.19 (VDD), U3.32 (VDD), U3.48 (VDD), U3.64 (VDD); also elsewhere on the board
BOOT0: R12.2, U3.60 (BOOT0)
CAN_RX: U3.44 (PA11); also elsewhere on the board
CAN_TX: U3.45 (PA12); also elsewhere on the board
CELL1_INT: U3.57 (PB5); also elsewhere on the board
CELL1_STAT: U3.56 (PB4); also elsewhere on the board
CELL2_INT: U3.51 (PC10); also elsewhere on the board
CELL2_STAT: U3.52 (PC11); also elsewhere on the board
GND: C25.1, C26.1, C27.1, C28.1, C29.1, C30.1, C31.1, C33.1, C34.2, C39.1, C40.1, C41.1, C42.1, FB1.2, J1.3, J2.3 (GND), J2.5 (GND), J2.9 (GNDDetect), PS1.2 (GND), PS1.4 (NC), S1.2, S1.3, U3.12 (VSSA), U3.18 (VSS), U3.31 (VSS), U3.47 (VSS), U3.63 (VSS); also elsewhere on the board
HEATER1_SWITCH_EN: U3.54 (PD2); also elsewhere on the board
HEATER2_SWITCH_EN: U3.40 (PC9); also elsewhere on the board
I2C1_SCL: R15.1, U3.58 (PB6); also elsewhere on the board
I2C1_SDA: R13.1, U3.59 (PB7); also elsewhere on the board
I2C2_SCL: R14.1, U3.29 (PB10); also elsewhere on the board
I2C2_SDA: R16.1, U3.30 (PB11); also elsewhere on the board
NRST: C27.2, S1.1, U3.7 (NRST)
unnamed: C23.1, C24.1
unnamed: J1.2, R12.1
unnamed: C41.2, C42.2, FB2.1, PS1.5 (OUT)
RCC_OSC_IN: C23.2, R11.1, U3.5 (PD0), Y1.2
RCC_OSC_OUT: C24.2, R11.2, U3.6 (PD1), Y1.1
SYS_JTDI: J2.8 (NC/TDI), U3.50 (PA15)
SYS_JTDO-TRACESWO: J2.6 (SWO/TDO), U3.55 (PB3)
SYS_JTICK-SWCLK: J2.4 (SWCLK/TCK), U3.49 (PA14)
SYS_JTMS-SWDIO: J2.2 (SWDIO/TMS), U3.46 (PA13)
SYS_NJTRST: J2.10 (~RESET)
VCC_BALANCE: C39.2, C40.2, PS1.1 (IN), PS1.3 (EN); also elsewhere on the board
Vbalance_sense_alert: U3.53 (PC12); also elsewhere on the board
Vbat_sense_alert: U3.27 (PB1); also elsewhere on the board

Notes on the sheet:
i2c1->chargers i2c2->current sense
LDO
VDDA pin decoupling caps+ 600ohm@100MHz(0.5A)

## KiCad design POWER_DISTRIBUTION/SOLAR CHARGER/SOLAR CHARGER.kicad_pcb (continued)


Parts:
C35: 100nF @50V; C_0402_1005Metric_Pad0.74x0.62mm_HandSolder
IC3: INA232AIDDFR; SOT65P280X110-8N; Mouser Part Number 595-INA232AIDDFR
R17: WSLP08059L000FEA18; RESC2013X58N; Mouser Part Number 71-WSLP08059L000FEA1

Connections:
+3.3V: C35.2, IC3.4 (VS); also elsewhere on the board
GND: C35.1, IC3.3 (GND), IC3.7 (A0); also elsewhere on the board
I2C1_SCL: IC3.5 (SCL); also elsewhere on the board
I2C1_SDA: IC3.6 (SDA); also elsewhere on the board
VCC_BALANCE: IC3.1 (IN+), IC3.2 (IN-), R17.1, R17.2; also elsewhere on the board
Vbalance_sense_alert: IC3.8 (ALERT); also elsewhere on the board

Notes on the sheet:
RC filters were not included due to the excessive power
Vbalance current sense: Rshunt< Vsenese/I max Vsense= ±81.92 mV (ADCRANGE = 0) , Imax=8.5 [max of charger], Rshunt=9.63764mohm Resistor power= (9.6e-03)*8.5^2=0.6936
RC 3db cut off freq: 100MHz
CURRENT SENSE_ Vbalance



Board: 4 copper layers, 85.0 x 55.0 mm, 138 parts (41 on the bottom side), 81 nets.

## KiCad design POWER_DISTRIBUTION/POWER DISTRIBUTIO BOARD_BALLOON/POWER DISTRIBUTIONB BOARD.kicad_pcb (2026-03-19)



Board: 4 copper layers, 94.5 x 55.0 mm, 98 parts (19 on the bottom side), 48 nets.

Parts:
C9, C10: 1uF @50V; C_0805_2012Metric_Pad1.18x1.45mm_HandSolder
C13, C15, C17, C19, C21, C22, C23, C24: 10uF@16V; C_0805_2012Metric_Pad1.18x1.45mm_HandSolder
C14, C20, C50, C52: 1uF; C_0603_1608Metric
C16, C18, C48, C49, C51, C54: 100nF; C_0603_1608Metric
C47: 100nF @50V; C_0402_1005Metric_Pad0.74x0.62mm_HandSolder
C53: 4.7nF; C_0603_1608Metric
D1, D2, D8, D10, D12, D13: BAS21; SOT-23
D5, D6: SMBJ12CA; DIONM5436X244N
D11: PESD2CANFD24V-UX; SOT65P210X110-3N
D14, D15: PESD3V3Z1BCSFYL; PMEG3005AESFYL
F2: 0154005.DRL; 0154005DRL
FB1: BLM21PG221SN1D; BEADC2012X105N
H5, H6, H7, H8: MountingHole_Pad; MountingHole_2.2mm_M2_ISO7380_Pad
IC3, IC4: TPS1HB08BQPWPRQ1; SOP65P640X120-17N
IC8: INA232AIDDFR; SOT65P280X110-8N
IC9: TCAN1044VDDFR; SOT65P280X110-8N
J8, J9, J10, J29, J30, J31: Conn_01x02; JST_PH_B2B-PH-K_1x02_P2.00mm_Vertical
J11: Conn_01x02; AMASS_XT30U-F_1x02_P5.0mm_Vertical
J28: Conn_01x06; JST_PH_B6B-PH-K_1x06_P2.00mm_Vertical
J32: Conn_01x04; JST_PH_B4B-PH-K_1x04_P2.00mm_Vertical
J33, J34: Conn_01x02; JST_PH_S2B-PH-K_1x02_P2.00mm_Horizontal
J35, J36: Conn_01x03; JST_PH_B3B-PH-K_1x03_P2.00mm_Vertical
PS3: RPMA5.0-4.5_OF; RPMA5045OF
PS4: TLV75733PDBVR; SOT95P280X145-5N
Q3, Q4: RSS070N05HZGTB; SOIC127P600X175-8N
R3, R4, R8, R9, R10, R11, R15, R16: 15k; R_0603_1608Metric
R5, R12, R62: 1K; R_0603_1608Metric
R6, R13: 4.7k; R_0603_1608Metric
R7, R14: 13.3k; R_0603_1608Metric
R42, R44: 10M; R_0603_1608Metric
R43, R45: 2k; R_0603_1608Metric
R52: WSHM28186L800FEA; WSHM2818R0330FEB
R53: 10K; R_0603_1608Metric
R54, R55, R63, R64: 2K4; R_0603_1608Metric
R56, R57: 4k7; R_0603_1608Metric
R58, R59: 60; R_0603_1608Metric
S2: OS102011MA1QN1
TP10: S2761-46R; TestPoint_Pad_1.5x1.5mm
TP11, TP27, TP28, TP29, TP30: S2761-46R; TestPoint_Pad_2.0x2.0mm
U6: ESP32-WROOM-32E; ESP32-WROOM-32D
U7: USBLC6-2SC6; SOT-23-6

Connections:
12V_BUS1: IC4.6 (VOUT_1), IC4.7 (VOUT_2), IC4.8 (VOUT_3), IC4.9 (VOUT_4), IC4.10 (VOUT_5), IC4.11 (VOUT_6), J10.1, TP28.1
12V_BUS2: IC3.6 (VOUT_1), IC3.7 (VOUT_2), IC3.8 (VOUT_3), IC3.9 (VOUT_4), IC3.10 (VOUT_5), IC3.11 (VOUT_6), J8.1, TP29.1
+3.3V: C47.2, IC8.4 (VS)
+3V3: C18.2, C48.2, C49.1, C50.1, C51.1, C52.1, D15.1 (K1), FB1.2, IC9.3 (VCC), J28.1, J32.1, J35.1, J36.1, R53.2, R54.1, R55.1, R56.1, R57.1, R63.1, R64.1, S2.3, TP30.1, U6.2 (VDD), U6.3 (EN), U7.5 (VBUS)
+5V0: C14.1, C16.1, C21.2, C22.2, C23.2, C24.2, D10.3 (K), D12.3 (K), D13.3 (K), J9.1, J30.1, J31.1, PS3.7 (+SENSE), PS3.8 (+VOUT), PS4.1 (IN), PS4.3 (EN), TP27.1
BOOT: D14.1 (K1), R62.2, U6.25 (IO0)
CAN+: D11.2 (K2), IC9.7 (CANH), J29.1, R58.2
CAN-: D11.1 (K1), IC9.6 (CANL), J29.2, R59.1
CAN_RX: IC9.4 (RXD), U6.26 (IO4)
CAN_TX: IC9.1 (TXD), U6.29 (IO5)
CUTTER_EN: J28.4, U6.6 (IO34)
GND: C9.1, C10.1, C13.1, C14.2, C15.1, C16.2, C17.1, C18.1, C19.1, C20.2, C21.1, C22.1, C23.1, C24.1, C47.1, C48.1, C49.2, C50.2, C51.2, C52.2, C53.2, C54.2, D1.3 (K), D2.3 (K), D5.1, D6.1, D8.1 (A), D10.1 (A), D11.3 (CC), D12.1 (A), D13.1 (A), D14.2 (K2), D15.2 (K2), H5.1, H6.1, H7.1, H8.1, IC8.3 (GND), IC8.7 (A0), IC9.2 (GND), IC9.8 (STB), J8.2, J9.2, J10.2, J11.2, J28.6, J30.2, J31.2, J32.4, J35.3, J36.3, PS3.3 (-VIN), PS3.4 (-VOUT), PS4.2 (GND), PS4.4 (NC), Q3.1 (SOURCE_1), Q3.2 (SOURCE_2), Q3.3 (SOURCE_3), Q4.1 (SOURCE_1), Q4.2 (SOURCE_2), Q4.3 (SOURCE_3), R3.1, R5.1, R6.2, R7.1, R8.2, R9.2, R10.1, R12.1, R13.2, R14.1, R15.2, R16.2, R42.1, R44.1, R53.1, S2.1, TP11.1, U6.1 (GND), U6.15 (GND), U6.38 (GND), U6.39 (GND), U7.2 (GND)
GPIO1_EN: R42.2, R43.2
GPIO2_EN: R44.2, R45.2
HEATER_EN: R11.1, U6.11 (IO26)
I2C2_SDA: IC8.6 (SDA), J28.3, R54.2, U6.8 (IO32)
I2C2_SDL: IC8.5 (SCL), J28.2, R55.2, U6.9 (IO33)
I2C_SDA: R63.2, U6.33 (IO21)
I2C_SDL: R64.2, U6.36 (IO22)
unnamed: C53.1, R58.1, R59.2
unnamed: D1.1 (A), IC3.1 (GND), R6.1
unnamed: D2.1 (A), IC4.1 (GND), R13.1
unnamed: IC3.16 (DIA_EN), R8.1
unnamed: IC3.4 (EN), R4.2
unnamed: IC3.5 (ILIM), R7.2
unnamed: IC3.3 (LATCH), R3.2
unnamed: IC3.14 (SEL1), R9.1
unnamed: IC3.2 (SNS), R5.2
unnamed: IC4.16 (DIA_EN), R15.1
unnamed: IC4.4 (EN), R11.2
unnamed: IC4.5 (ILIM), R14.2
unnamed: IC4.3 (LATCH), R10.2
unnamed: IC4.14 (SEL1), R16.1
unnamed: IC4.2 (SNS), R12.2
unnamed: C20.1, C54.1, FB1.1, PS4.5 (OUT)
unnamed: D6.2, Q3.4 (GATE), R45.1
unnamed: D5.2, Q4.4 (GATE), R43.1
unnamed: R62.1, S2.2
PGM_RX: J32.2, U6.35 (TXD0/IO1), U7.1 (I/O1), U7.6 (I/O1)
PGM_TX: J32.3, U6.34 (RXD0/IO3), U7.3 (I/O2), U7.4 (I/O2)
PYR_1: J33.1, Q4.5 (DRAIN_1), Q4.6 (DRAIN_2), Q4.7 (DRAIN_3), Q4.8 (DRAIN_4)
PYR_2: J34.1, Q3.5 (DRAIN_1), Q3.6 (DRAIN_2), Q3.7 (DRAIN_3), Q3.8 (DRAIN_4)
VBAT+: C9.2, C10.2, D8.3 (K), F2.1, IC3.17 (VBB), IC4.17 (VBB), J11.1, TP10.1
VBAT_Fused: C13.2, C15.2, C17.2, C19.2, F2.2, IC8.1 (IN+), PS3.1 (+VIN), R52.2
VBAT_Fused_OUT: IC8.2 (IN-), J33.2, J34.2, R52.1
VTX_EN: J28.5, R4.1, U6.7 (IO35)
onewire1: J35.2, R56.2, U6.10 (IO25)
onewire2: J36.2, R57.2, U6.37 (IO23)

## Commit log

2026-02-23 added everytrhing
    [MP2731 (QFN-26, 3.5x3.5).step, MP3429GL.step, PDB_BALANCER.kicad_sch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]
2026-03-19 commit after disaster
    [POWER DISTRIBUTIONB BOARD.kicad_pcb]
2026-06-28 addition of UREX pDB
    [PIC.kicad_sch, UREX_PDB.kicad_pcb, UREX_PDB.kicad_sch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]
2026-06-28 CONFIGURED LIBARY PATHS FOR UREX_PDB
    [UREX_PDB.kicad_pcb]
2026-06-29 FIXED LIBRARY
    [PIC.kicad_sch, UREX_PDB.kicad_pcb, UREX_PDB.kicad_sch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]

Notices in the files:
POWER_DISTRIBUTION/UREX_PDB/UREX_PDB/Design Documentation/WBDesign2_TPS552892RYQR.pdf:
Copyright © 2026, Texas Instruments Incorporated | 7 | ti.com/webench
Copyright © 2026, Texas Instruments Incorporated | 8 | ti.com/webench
